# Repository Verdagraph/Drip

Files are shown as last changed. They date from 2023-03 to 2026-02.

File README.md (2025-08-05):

<!-- PROJECT SHIELDS -->
<!--
*** I'm using markdown "reference style" links for readability.
*** Reference links are enclosed in brackets [ ] instead of parentheses ( ).
*** See the bottom of this document for the declaration of the reference variables
*** https://www.markdownguide.org/basic-syntax/#reference-style-links
-->

[][version-url]
[][issues-url]
[][prs-url]

<!-- PROJECT LOGO -->
<br />
<div align="center">
  <a href="https://github.com/Verdagraph">
    
  </a>

<h3 align="center">Verdagraph - Web Application</h3>

  <p align="center">
    A garden productivity tool, agro-ecology model, and IoT platform
    for a sustainable and cooperative future.
    <br />
    <!-- 
    <a href=""><strong>Try it yourself »</strong></a>
    <br />
    -->
    <br />
    <a href="https://verdagraph.org">Documentation</a>
    <!-- 
    ·
    <a href="https://youtu.be/jGFHhRVdxRM">YouTube</a>
    ·
    <a href="">Donate</a>
    --> 
    <br />
  </p>
</div>

See the [main project readme](https://github.com/Verdagraph) for background on this repository.

The Drip is an IoT irrigation controller intended to automate the management of fixed-pressure water supplies along with variable-pressure / gravitypfed rain catchement systems. Its current scope is to control dispensing water from one rain barrel and one fixed pressure supply, using a flow meter to track precise targets, and a pressure sensor to track the water level of the catchement system, and an ESP32.

This repository contains the ESP-IDF firmware, PCB design, BOM, and instructions for setting up the system. 

Possible improvements, in no particular order:
    - Creating a solar charging version with included circuitry and deep sleep mode.
    - Support using more than one of each type of water supply.
    - Control 12V pumps in case gravity-fed isn't possible.

## PCB Design

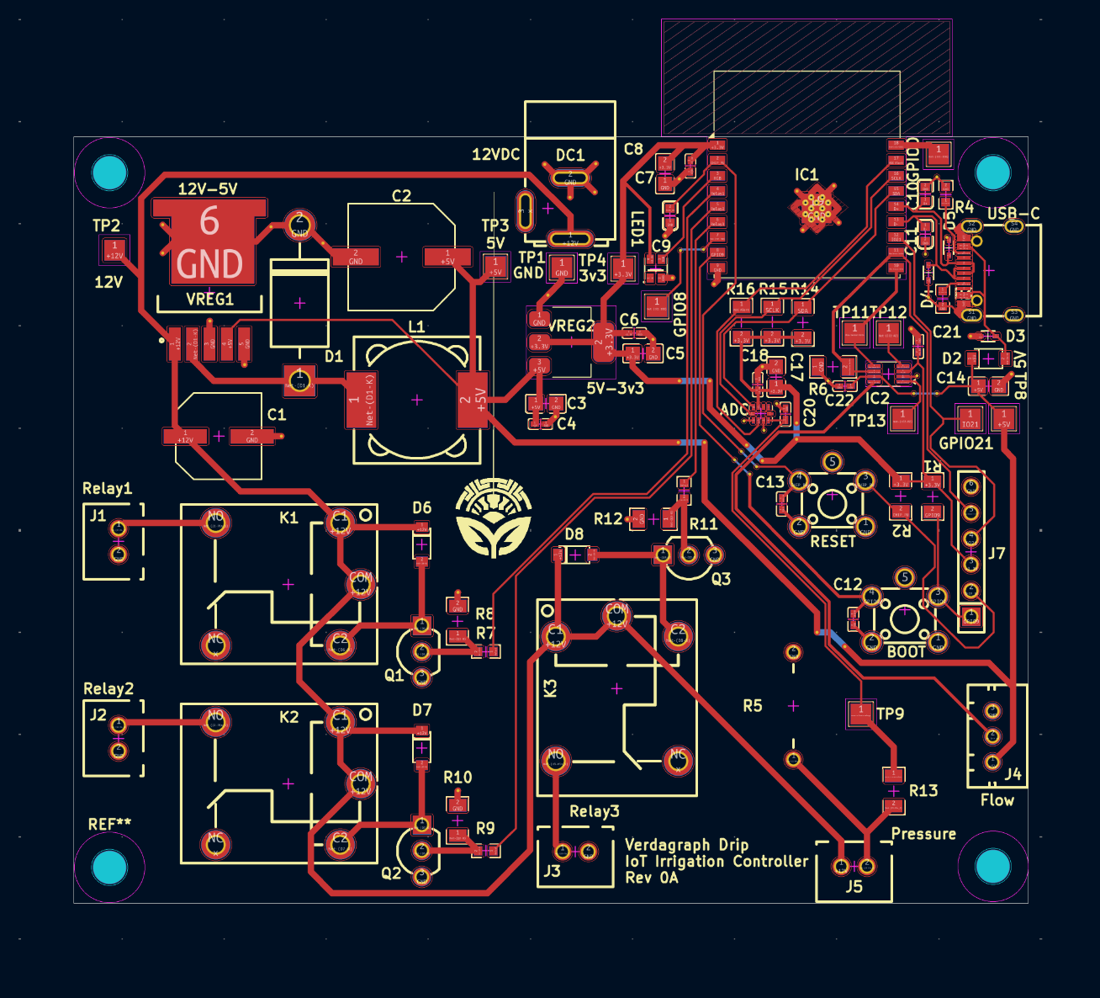
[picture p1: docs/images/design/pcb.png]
PCB Screenshot


## Firmware Design

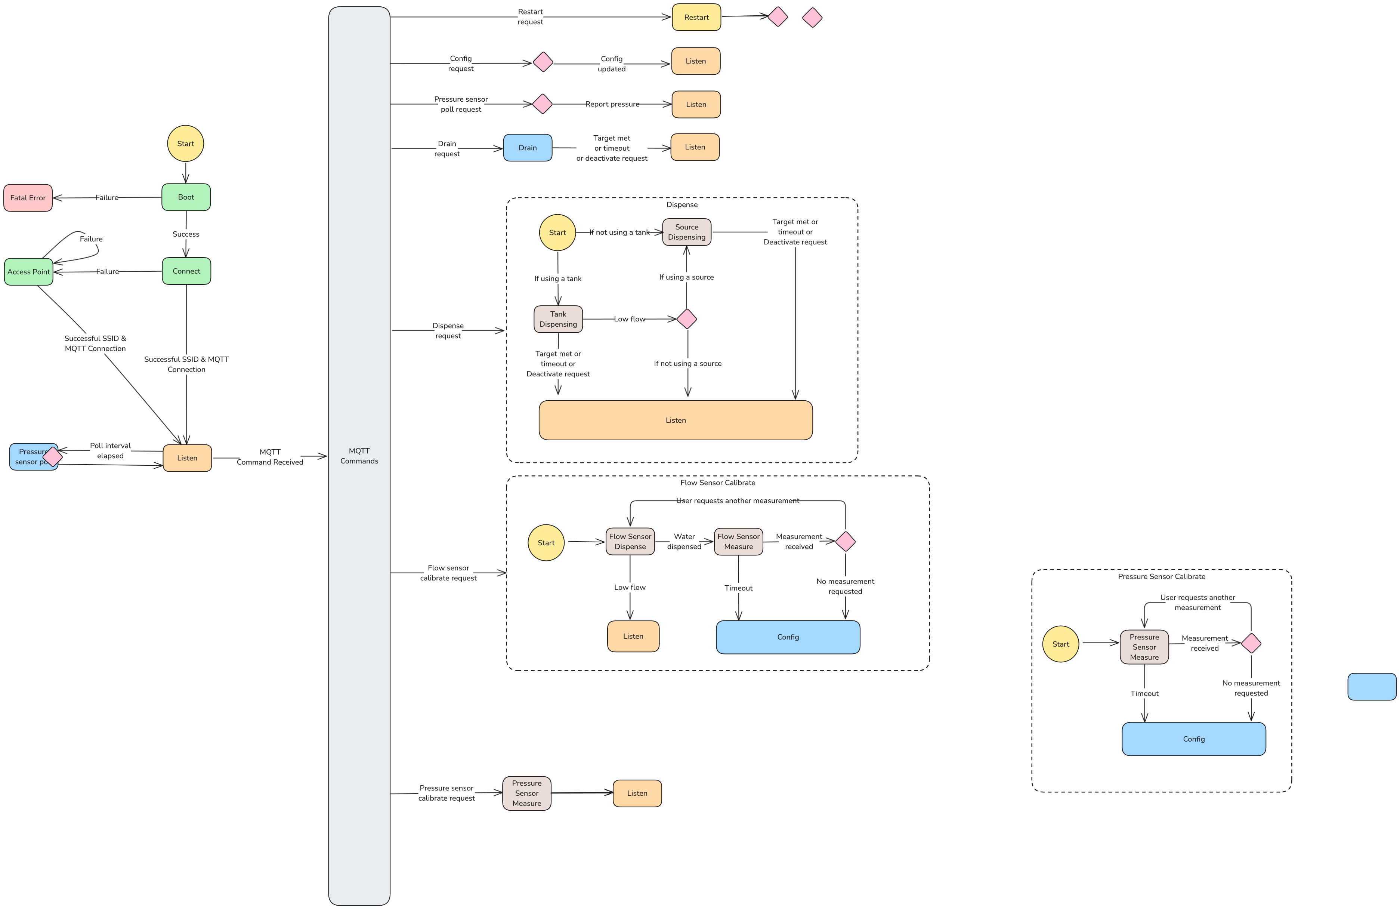
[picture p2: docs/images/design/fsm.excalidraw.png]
FSM Screenshot


# Contributing

See the [contributing](./contributing.md) for instructions on contributing and setting up the development environment.

<!-- MARKDOWN LINKS & IMAGES -->
<!-- https://www.markdownguide.org/basic-syntax/#reference-style-links -->

<!-- IN-REPO -->

[version-shield]: https://img.shields.io/badge/version-0.0.1-blue?style=for-the-badge
[version-url]: https://github.com/Verdagraph/Drip/releases
[issues-shield]: https://img.shields.io/github/issues/Verdagraph/Drip.svg?style=for-the-badge
[issues-url]: https://github.com/Verdagraph/Drip/issues
[prs-shield]: https://img.shields.io/github/issues-pr/Verdagraph/Drip.svg?style=for-the-badge
[prs-url]: https://github.com/Verdagraph/Drip/pulls
[license-shield]: https://img.shields.io/github/license/Verdagraph/Drip.svg?style=for-the-badge
[license-url]: https://github.com/Verdagraph/Drip/LICENSE.txt

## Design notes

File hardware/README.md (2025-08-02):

# PCB Design

https://www.electronics-tutorials.ws/blog/relay-switch-circuit.html
https://www.digikey.ca/en/blog/logic-level-shifting-basics  

There's two main type of pressure transducers: ones that have two wires and output a current, and ones that have 3 wires and output a voltage.
We can use the first type by adding a resistor with a known value to the path. Because we know the sensor is outputting a given current, and we know that the resistor must dissipate all the voltage before it as its connected to ground, we can take the voltage before the resistor and connect it to our ADC for a measurements.
The resistor is commonly 250 ohms which translates to 1-5V. For the voltage type, it is as simple as connecting the voltage to the ADC. For the current type, we measure the voltcage through a 10k ohm resistor, and remember that the 250 ohm resistor must sink the power (THT). We use a 220 ohm to give a little margin for error.

The reset button is connected to the CHIP_PU or chip power up pin on the ESP. It is pulled up by default, enabling the MCU. When the button is pressed it is pulled to GND, with a small filtering capacitor to smooth it out, and the device resets.

The boot button is connectod to GPIO9. When GPIO0 is pulled high, the chip will boot into its saved program. When its pulled low, it will enter into the USB/UART boot mode. This person (https://www.instructables.com/Build-Custom-ESP32-Boards-From-Scratch-the-Complet/) also added a pullup here and found it reduced boot errors.

The USBC receptable connects the positive and negative data terminals on either side together and shunts them along with the USB bus voltage with zener diodes for ESD protection and the schtokky diode on the voltage line for reverse current protection, along with a filtering capacitor. THe CC1 and CC2 lines are pulled down for USBC functinoality

To the microcontroller: the power line is again filtered so that the voltage regulators can be farther from the rest. The chip_pu is pulled up again and filtered. The USB data lines are filtered again as well. There is a common bug in the devkits where because the CHIP_EN pin is used to reset the chip, and the GPIO9 pin is used to select the boot mode, the GPIO9 pin must be high at least 3ms before the CHIP_EN pin to avoid puttin the board in boot. To accomplish this, we add a pullup to GPIO9 to get around the weak internal pullup. This works because the GPIO9 is pulled up to the 3v3 output of the regulator, but the CHIP_EN is only brouhgut up once the ESP's 3v3 rail stabalizes, and it has extra filtering capacitors so it takes longer.

Our 12v-5v regulator is a switching buck converter LM2575, the fixed 5V output version. According to the typical application circuit, it has a filtering capacitor on the input, an LC filter on the output. There is also a schtokky diode to ground which allows a path for the inductor transient response to dissipate. To choose the L we follow the datasheet. Vin - Vout = 12-5 = 7. Vin - Vout * Vout / Vin * 1000 / 52 = 56V x us. We use the figure 12 to find the intersection of this and 1A means 220uH is  good. To choose output cap we use the formula in the datasheet which yields 56 uF. This is only for stability though. For ripple We round up to 330. 

the 5V to 3.3V regulator is the AMS1117 linear regulator and it has the same 2 capacitor filter on either end with a power LED.

The relays. These are 5 terminal 5V relay modules. The coils need 5V and 360mw to turn on so they need .36 / 5 = 72ma to run. Except the CE has voltage at saturation so we factor in a 0.7V drop. We also double the minimum current we need to make sure it works which gives us 167mA. We need to drive it with a transistor to get the 5V signal. The relay has a flyback diode. We use the BC337 but assume the transistor to have abeta of at least 100 which will cover common transistors at these conditions. This gives us a base current of 1.67mA. Given we're using 3.3v to run this that means the voltage across the resistor must be (3.3V - VBE) = 3.3 - 1.2 (which is the max BE voltage on the BC337 and 2n2222a) = 2.1V. R = V / I = 2.1V / 1.67ma = 1254ohm rounded to 1000.

The flow sensor: we use the TX20102 logic level shifter to go between the 5V pulses of the flow sensor and the 3.3V logic of the ESP. The enable pin is pulled down and connected to a GPIO so we can disable the pulses into the microcontroller when we don't care about the flow. We also have 0.1uF filters to stabailize the reference voltages as much as possible.

The ADC is the ADC088S022, as the ESP ADC is not reliable. This has both the 5V and 3.3V lines as the analog and digital power lines with filtering. The I2C is used to communicate with the ESP, while the power lines are filted as well. The max that we can go on any input is the analog supply + 0.3V, meaning we shouldn't make it go beyond 5.3V

https://www.aliexpress.com/item/1005006568129795.html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

Power profiles:
ESP32c3 wroom 02: max 345A

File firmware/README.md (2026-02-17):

git clone --recursive <your-repo-url>

git submodule update --init --recursive

| Supported Targets | ESP32 | ESP32-C2 | ESP32-C3 | ESP32-C5 | ESP32-C6 | ESP32-C61 | ESP32-H2 | ESP32-H21 | ESP32-H4 | ESP32-P4 | ESP32-S2 | ESP32-S3 | Linux |
| --- | ----- | --- | --- | --- | --- | --- | --- | --- | --- | --- | --- | --- | ----- |

# Hello World Example

Starts a FreeRTOS task to print "Hello World".

(See the README.md file in the upper level 'examples' directory for more information about examples.)

## How to use example

Follow detailed instructions provided specifically for this example.

Select the instructions depending on Espressif chip installed on your development board:

- [ESP32 Getting Started Guide](https://docs.espressif.com/projects/esp-idf/en/stable/get-started/index.html)
- [ESP32-S2 Getting Started Guide](https://docs.espressif.com/projects/esp-idf/en/latest/esp32s2/get-started/index.html)

## Example folder contents

The project **hello_world** contains one source file in C language [hello_world_main.c](main/hello_world_main.c). The file is located in folder [main](main).

ESP-IDF projects are built using CMake. The project build configuration is contained in `CMakeLists.txt` files that provide set of directives and instructions describing the project's source files and targets (executable, library, or both).

Below is short explanation of remaining files in the project folder.

```
├── CMakeLists.txt
├── pytest_hello_world.py      Python script used for automated testing
├── main
│   ├── CMakeLists.txt
│   └── hello_world_main.c
└── README.md                  This is the file you are currently reading
```

For more information on structure and contents of ESP-IDF projects, please refer to Section [Build System](https://docs.espressif.com/projects/esp-idf/en/latest/esp32/api-guides/build-system.html) of the ESP-IDF Programming Guide.

## Troubleshooting

* Program upload failure

    * Hardware connection is not correct: run `idf.py -p PORT monitor`, and reboot your board to see if there are any output logs.
    * The baud rate for downloading is too high: lower your baud rate in the `menuconfig` menu, and try again.

## Technical support and feedback

Please use the following feedback channels:

* For technical queries, go to the [esp32.com](https://esp32.com/) forum
* For a feature request or bug report, create a [GitHub issue](https://github.com/espressif/esp-idf/issues)

We will get back to you as soon as possible.

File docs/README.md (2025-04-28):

# VerdanTech Drip - Open Source Drip Irrigation Controller

The VDT Drip is an open source irrigation controller based on the ESP8266. The Drip's main function is to dispense a given volume of water with irrigation systems that integrate variable-flow water supplies.

To do this, the Drip employs 1-3 solenoid valve(s), 0-1 flow sensor(s), 0-1 pressure sensor(s), and communication via an MQTT broker.

## Project Instructions

1. Read the [terminology](#terminology) and [interface](#mqtt-interface) sections 
to understand the device's capabilities and limitations.

2. Read the [hardware](#hardware) section and decide on an operating mode.

3. Secure the use of an MQTT broker

4. Source [materials](#equipment-1)

5. [Assemble](#assembly) the device

6. Install the Arduino platform, required libraries, and board drivers

7. Configure the device through the file `config.h`

8. Flash the microcontroller with the software

9. Connect to a WiFi network and MQTT broker through the auto-connect access point

10. Calibrate flow sensor

## Terminology

Refer to this list for explicit descriptions of some key terms used throughout the document.

### Water Supplies

- **Source**
    - A supply of water that is assumed to be inexhaustible with a static or variable flow rate, such as a utility water supply.
- **Tank**
    - A supply of water that is assumed to be exhaustible with a variable flow rate, such as a rain barrel.

### Equipment

For specific product examples see the [equipment](#equipment) section.

- **Valve**
    - An electronically controllable water valve, such as a solenoid valve.
- **Flow sensor**
    - A water flow sensor capable of sending a steady rate of electrical pulses per unit volume, such as a hall effect flow sensor.
- **Pressure sensor**
    - A pressure sensor capable of sending an absolute pressure reading through I2C and of surviving the maximum water pressure in the **Tank**.
- **Operational mode**
    - A specific combination of source, tank, valves, flow sensor, and pressure sensor, as described in the [hardware](#operating-modes) section.

### Software

- **MQTT**
    - A network protocol used for internet-of-things (IOT) devices. See [wiki](https://en.wikipedia.org/wiki/MQTT).

### Operation

- **Dispense**
    - A process of attempting to output a target volume of water, first from the tank, then from the source.
- **Drain**
    - A process of attempting to release water from the tank without it going to the usual intended output, to prevent overflow, or to get rid of stale water.

## MQTT interface

This section describes the functionality of the MQTT topics through which the device sends and recieves information. All communication is done via JSON. For topics which are subscribed to by the controller, a list of inputs is described for each topic, and for topics which are published by the controller, a list of outputs are described for each topic. Inputs are marked (optional) if the  function will still be carried out if they aren't included rather than throw an error. Inputs are marked (conditional) if they only have effect based on [configuration settings](#configuration), and outputs are marked (conditional) if their inclusion in the payload is dependent on [configuration settings](#configuration).

| Title | Topic string config  | Does the controller publish or subscribe? | Is the topic enabled unconditionally? |
| --- | --- | --- | --- |
| [Dispense activate](#activation)  | [`DISPENSE_ACTIVATE_TOPIC_`](#auto-config) | Subscribe | Yes |
| [Dispense slice report](#slice-reporting)  | [`DISPENSE_REPORT_SLICE_TOPIC_`](#auto-config)  | Publish | Yes |
| [Dispense summary report](#summary-reporting)  | [`DISPENSE_REPORT_SUMMARY_TOPIC_`](#auto-config)  | Publish | Yes |
| [Deactivate](#deactivation)  | [`DEACTIVATE_TOPIC_`](#auto-config)  | Subscribe | Yes |
| [Restart](#restart)  | [`RESTART_TOPIC_`](#auto-config)  | Subscribe | Yes |
| [Info logging](#info)  | [`LOG_TOPIC_`](#auto-config)  | Publish | Yes |
| [Warning logging](#warnings)  | [`WARNING_TOPIC_`](#auto-config)  | Publish | Yes |
| [Error logging](#errors)  | [`ERROR_TOPIC_`](#auto-config)  | Publish | Yes |
| [Read config](#read)  | [`CONFIG_TOPIC_`](#auto-config)  | Publish | Yes |
| [Read auto-config](#read-auto-config)  | [`AUTO_CONFIG_TOPIC_`](#auto-config)  | Publish | Yes |
| [Read topic config](#read-topic-config)  | [`TOPIC_CONFIG_TOPIC_`](#auto-config)  | Publish | Yes |
| [Write config](#write)  | [`CONFIG_CHANGE_TOPIC_`](#auto-config)  | Subscribe | Yes |
| [Reset settings](#reset-settings)  | [`SETTINGS_RESET_TOPIC_`](#auto-config)  | Subscribe | Yes |
| [Flow sensor calibrate begin](#begin) | [`FLOW_SENSOR_CALIBRATE_BEGIN`](#auto-config) | Subscribe | No |
| [Flow sensor calibrate dispense](#dispense) | [`FLOW_SENSOR_CALIBRATE_DISPENSE`](#auto-config) | Subscribe | No |
| [Flow sensor calibrate measure](#measure) | [`FLOW_SENSOR_CALIBRATE_MEASURE`](#auto-config) | Subscribe | No |
| [Drain activate](#activation-1)  | [`DRAIN_ACTIVATE_TOPIC_`](#auto-config)  | Subscribe | No |
| [Drain summary report](#reporting)  | [`DRAIN_REPORT_SUMMARY_TOPIC_`](#auto-config)  | Publish | No |
| [Pressure report request](#request)  | [`PRESSURE_REQUEST_TOPIC_`](#auto-config) | Subscribe | No |
| [Pressure report](#report) | [`PRESSURE_REPORT_TOPIC_`](#auto-config) | Publish | No |

### Dispense

The main functionality of the device. The dispentation topics handle setting target volumes for the dispense process, publishing data taken at regular intervals through the process, and publishing data at the end of the process.

#### Activation

| Topic string config  | Publish or subscribe? | Enabled unconditionally? |
| --- | --- | --- |
| [`DISPENSE_ACTIVATE_TOPIC_`](#auto-config)  | Subscribe | Yes |

This topic allows activating the dispense process and setting the target volume. Activation will fail if a dispense process or drain process is already in progress. The dispense process will continue until the output volume is greater than or equal to the target volume, or a singularly connected tank produces a flow rate less than that defined by [`FlowSensorConfig.min_flow_rate`](#runtime-config) and the current duration of the process is greater than that defined by [`TankConfig.tank_timeout`](#runtime-config). If the tank is connected with a source, then the dispense will switch to the source until the target volume is reached.

Inputs:
- `["tv"]` float. Target volume of the dispense process in liters.

Sample payload:
```
{
  "tv": 10.25
}
```

#### Slice Reporting

| Topic string config  | Publish or subscribe? | Enabled unconditionally? |
| --- | --- | --- |
| [`DISPENSE_REPORT_SLICE_TOPIC_`](#auto-config)  | Publish | Yes |

This topic is where the mid-process datapoints on the dispense process are published at a volume interval in liters defined by [`ServicesConfig.data_resolution_l`](#runtime-config). If the connection to the MQTT broker fails, these reports will fail to be sent and are lost, but the dispense process will continue. Unfortunately, the [MQTT client](#dependencies) class is only able to send messages at a quality-of-service of 0. 

Outputs:
- `["t"]` float. Current duration of the dispense process in seconds.
- `["v"]` float. Current output volume of the dispense process in liters.
- `["q"]` float. The average flow rate of output volume calculated either from the last slice report to the current one (or from the beginning of the process if on the first report) in liters per minute
- `["tp"]` (conditional) float. The average tank gauge pressure calculated from the last slice report to the current one (or from the beginning of the process if on the first report) in hectopascals. Enabled if [`USING_PRESSURE_SENSOR_`](#auto-config) and [`PressureSensorConfig.report_mode`](#runtime-config) equals 1 or 3.
- `["tv"]` (conditional) float. The average tank volume calculated from the last slice report to the current one (or from the beginning of the process if on the first report) in liters. Enabled if [`USING_PRESSURE_SENSOR_`](#auto-config) and [`PressureSensorConfig.report_mode`](#runtime-config) equals 2 or 3. Ensure that the [tank geometry](#runtime-config) is properly configured.

Sample payload:
```
{
  "t": 5000,
  "v": 0.1,
  "q": 13.2,
  "tp": 68.94,
  "tv": 85.6
}
```

#### Summary Reporting

| Topic string config  | Publish or subscribe? | Enabled unconditionally? |
| --- | --- | --- |
| [`DISPENSE_REPORT_SUMMARY_TOPIC_`](#auto-config)  | Publish | Yes |

This topic is where the post-process datapoints on the dispense process are published. If the connection to the MQTT broker fails, the connection is re-tried once before the message is lost.  Unfortunately, the [MQTT client](#dependencies) class is only able to send messages at a quality-of-service of 0.

Outputs:
- `["tt"]` float. Total duration of the dispense process in seconds.
- `["vt"]` float. Total output volume of the dispense process in liters.
- `["tv"]` (conditional) float. The total output volume produced by the tank in liters. Enabled if [`USING_TANK_`](#auto-config).
- `["tts"]` (conditional) int. The time stamp at which the dispense process switched from the tank to the source. Will equal `["tt"]` if the processes ended without switching water supplies. Enabled if [`USING_TANK_`](#auto-config) and [`USING_SOURCE_`](#auto-config).

Sample payload:
```
{
  "tt": 50,
  "vt": 10.25,
  "tv": 5.6,
  "tts": 250000,
}
```

### Deactivation

| Topic string config  | Publish or subscribe? | Enabled unconditionally? |
| --- | --- | --- |
| [`DEACTIVATE_TOPIC_`](#auto-config)  | Subscribe | Yes |

This topic is where commands for deactivating current processes are sent. Any message recieved on this topic will trigger the deactivation regardless of payload. Upon reception, the device will close all valves, end all ongoing dispense or drain processes, and send summary reports of any ongoing processes.

Inputs: None.

Sample payload:
```
{}
```

### Restart

| Topic string config  | Publish or subscribe? | Enabled unconditionally? |
| --- | --- | --- |
| [`RESTART_TOPIC_`](#auto-config)  | Subscribe | Yes |

This topic is where requests for restarting the controller are sent. Any message recieved on this topic will trigger the restart regardless of payload. Upon reception, the device will power down and restart, right after sending the reports for any processes in progress.

Inputs: None.

Sample payload:
```
{}
```

### Logging

These topics are where the device will send status logs alongside events and changes in state.

#### Info

| Topic string config  | Publish or subscribe? | Enabled unconditionally? |
| --- | --- | --- |
| [`LOG_TOPIC_`](#auto-config)  | Publish | Yes |

This topic is where the device sends status logs that aren't warnings or errors. Once connected to the MQTT broker, most status changes are reflected here. 

Outputs:
- `["m"]` string. The info log message.

Sample payload:
```
{
  "m": "Beginning dispense process with target volume: 10.25 liters"
}
```

#### Warnings

| Topic string config  | Publish or subscribe? | Enabled unconditionally? |
| --- | --- | --- |
| [`WARNING_TOPIC_`](#auto-config)  | Publish | Yes |

This topic is where the device sends status logs about events that don't break things but may result in abnormal function.

Outputs:
- `["m"]` string. The warning log message.

Sample payload:
```
{
  "m": "Flow rate exceeded maximum"
}
```

#### Errors

| Topic string config  | Publish or subscribe? | Enabled unconditionally? |
| --- | --- | --- |
| [`ERROR_TOPIC_`](#auto-config)  | Publish | Yes |

This topic is where the device sends status logs about events that prevent sucessful function.

Outputs:
- `["m"]` string. The error log message.

Sample payload:
```
{
  "m": "Dispense request denied, process already in progress."
}
```

### Config

These topics allow viewing and updating configuration settings at runtime, and viewing the hard-coded auto-configs. The available settings are listed as [config defaults](#defaults). 

#### Read

| Topic string config  | Publish or subscribe? | Enabled unconditionally? |
| --- | --- | --- |
| [`CONFIG_TOPIC_`](#auto-config)  | Publish | Yes |

This topic is where the device will send the current configuration values. It sends a retained message containing all values on startup and every time the configuration is changed.

Outputs:
- `["srvc"]["res"]` float. The value of [`ServicesConfig.data_resolution_l`](#runtime-config).
- `["src"]["rate"]` (conditional) float. The value of [`SourceConfig.static_flow_rate`](#runtime-config). Enabled if [`USING_SOURCE_`](#auto-config).
- `["tnk"]["time"]` (conditional) int. The value of [`TankConfig.tank_timeout`](#runtime-config). Enabled if [`USING_TANK_`](#auto-config).
- `["tnk"]["shape"]` (conditional) int. The value of [`TankConfig.shape_type`](#runtime-config). Enabled if [`USING_TANK_`](#auto-config).
- `["tnk"]["dim1"]` (conditional) float. The value of [`TankConfig.dimension_1`](#runtime-config). Enabled if [`USING_TANK_`](#auto-config).
- `["tnk"]["dim2"]` (conditional) float. The value of [`TankConfig.dimension_2`](#runtime-config). Enabled if [`USING_TANK_`](#auto-config).
- `["tnk"]["dim3"]` (conditional) float. The value of [`TankConfig.dimension_3`](#runtime-config). Enabled if [`USING_TANK_`](#auto-config).
- `["flow"]["ppl"]` (conditional) float. The value of [`FlowSensorConfig.pulses_per_l`](#runtime-config). Enabled if [`USING_FLOW_SENSOR_`](#auto-config).
- `["flow"]["max"]` (conditional) float. The value of [`FlowSensorConfig.max_flow_rate`](#runtime-config). Enabled if [`USING_FLOW_SENSOR_`](#auto-config).
- `["flow"]["min"]` (conditional) float. The value of [`FlowSensorConfig.min_flow_rate`](#runtime-config). Enabled if [`USING_FLOW_SENSOR_`](#auto-config).
- `["flow"]["time"]` (conditional) float. The value of [`FlowSensorConfig.calibration_timeout`](#runtime-config). Enabled if [`USING_FLOW_SENSOR_`](#auto-config).
- `["flow"]["cmax"]` (conditional) float. The value of [`FlowSensorConfig.calibration_max_volume`](#runtime-config). Enabled if [`USING_FLOW_SENSOR_`](#auto-config).
- `["prssr"]["mode"]` (conditional) int. The value of [`PressureSensorConfig.report_mode`](#runtime-config). Enabled if [`USING_PRESSURE_SENSOR_`](#auto-config).
- `["prssr"]["atmo"]` (conditional) float. The value of [`PressureSensorConfig.atmosphere_pressure`](#runtime-config). Enabled if [`USING_PRESSURE_SENSOR_`](#auto-config).
- `["auto"]["src"]` float. The value of [`USING_SOURCE_`](#auto-config).

Sample payload:
```
```

#### Read Auto-Config

| Topic string config  | Publish or subscribe? | Enabled unconditionally? |
| --- | --- | --- |
| [`AUTO_CONFIG_TOPIC_`](#auto-config)  | Publish | Yes |

This topic is where the device will send the hard-coded [auto-config](#auto-config) values, in a retained message. This topic is published to only on startup.

Outputs:
- `["src"]` bool. The value of [`USING_SOURCE_`](#auto-config).
- `["tnk"]` bool. The value of [`USING_TANK_`](#auto-config).
- `["drn"]` bool. The value of [`USING_DRAIN_VALVE_`](#auto-config).
- `["flow"]` bool. The value of [`USING_FLOW_SENSOR_`](#auto-config).
- `["prssr"]` bool. The value of [`USING_PRESSURE_SENSOR_`](#auto-config).
- `["srcpin"]` int. The value of [`SOURCE_OUTPUT_VALVE_PIN_`](#auto-config).
- `["tnkpin"]` int. The value of [`TANK_OUTPUT_VALVE_PIN_`](#auto-config).
- `["drnpin"]` int. The value of [`TANK_DRAIN_VALVE_PIN_`](#auto-config).
- `["flowpin"]` int. The value of [`FLOW_SENSOR_PIN_`](#auto-config).

Sample payload:
```
```

#### Read Topic Config

| Topic string config  | Publish or subscribe? | Enabled unconditionally? |
| --- | --- | --- |
| [`TOPIC_CONFIG_TOPIC_`](#auto-config)  | Publish | Yes |

This topic is where the device wil send the hard-coded [topic strings](#topics), in a retained message. Keep in mind that the strings are sent as they are before the appendment to [`BASE_TOPIC`](#topics), in order to minimize payload size. This topic is published to only on startup.

Outputs:
- `["base"]` string. The value of ['BASE_TOPIC'](#topics).
- `["out"]` string. The value of ['DISPENSE_ACTIVATE_TOPIC'](#topics).
- `["out_slice"]` string. The value of ['DISPENSE_REPORT_SLICE_TOPIC'](#topics).
- `["out_summary"]` string. The value of ['DISPENSE_REPORT_SUMMARY_TOPIC'](#topics).
- `["deactivate"]` string. The value of ['DEACTIVATE_TOPIC'](#topics).
- `["restart"]` string. The value of ['RESTART_TOPIC'](#topics).
- `["log"]` string. The value of ['LOG_TOPIC'](#topics).
- `["warning"]` string. The value of ['WARNING_TOPIC'](#topics).
- `["error"]` string. The value of ['ERROR_TOPIC'](#topics).
- `["config"]` string. The value of ['CONFIG_TOPIC'](#topics).
- `["auto"]` string. The value of ['AUTO_CONFIG_TOPIC'](#topics).
- `["topics"]` string. The value of ['TOPIC_CONFIG_TOPIC'](#topics).
- `["conf_write"]` string. The value of ['CONFIG_CHANGE_TOPIC'](#topics).
- `["conf_reset"]` string. The value of ['SETTINGS_RESET_TOPIC'](#topics).
- `["cbr_on"]` (conditional) string. The value of ['FLOW_SENSOR_CALIBRATE_BEGIN_TOPIC'](#topics). Enabled if [`USING_FLOW_SENSOR_`](#auto-config).
- `["cbr_out"]` (conditional) string. The value of ['FLOW_SENSOR_CALIBRATE_DISPENSE_TOPIC'](#topics). Enabled if [`USING_FLOW_SENSOR_`](#auto-config).
- `["cbr_measure"]` (conditional) string. The value of ['FLOW_SENSOR_CALIBRATE_MEASURE_TOPIC'](#topics). Enabled if [`USING_FLOW_SENSOR_`](#auto-config).
- `["drn"]` (conditional) string. The value of ['DRAIN_ACTIVATE_TOPIC'](#topics). Enabled if [`USING_DRAIN_`](#auto-config).
- `["drn_summary"]` (conditional) string. The value of ['DRAIN_REPORT_SUMMARY_TOPIC'](#topics). Enabled if [`USING_DRAIN_`](#auto-config).
- `["prssr_request"]` (conditional) string. The value of ['PRESSURE_REQUEST_TOPIC'](#topics). Enabled if [`USING_PRESSURE_SENSOR_`](#auto-config).
- `["prssr"]` (conditional) string. The value of ['PRESSURE_REPORT_TOPIC'](#topics). Enabled if [`USING_PRESSURE_SENSOR_`](#auto-config).

Sample payload:
```
```

#### Write

| Topic string config  | Publish or subscribe? | Enabled unconditionally? |
| --- | --- | --- |
| [`CONFIG_CHANGE_TOPIC_`](#auto-config)  | Subscribe | Yes |

This topic is where the device will accept changes to the configuration values. All the inputs are optional, meaning any combination of inputs will be accepted, and only the settings that are to be changed must be sent. Upon reception of the message, the device will update the [config structs](#runtime-config), write the new values to the file system, and publish the new values to [`CONFIG_TOPIC_`](#auto-config).

Inputs:
- `["srvc"]["res"]` (optional) float. The value of [`ServicesConfig.data_resolution_l`](#runtime-config) to be set.
- `["src"]["rate"]` (optional, conditional) float. The value of [`SourceConfig.static_flow_rate`](#runtime-config) to be set.
- `["tnk"]["time"]` (optional, conditional) int. The value of [`TankConfig.tank_timeout`](#runtime-config) to be set.
- `["tnk"]["shape"]` (optional, conditional) int. The value of [`TankConfig.shape_type`](#runtime-config) to be set.
- `["tnk"]["dim1"]` (optional, conditional) float. The value of [`TankConfig.dimension_1`](#runtime-config) to be set.
- `["tnk"]["dim2"]` (optional, conditional) float. The value of [`TankConfig.dimension_2`](#runtime-config) to be set.
- `["tnk"]["dim3"]` (optional, conditional) float. The value of [`TankConfig.dimension_3`](#runtime-config) to be set.
- `["flow"]["ppl"]` (optional, conditional) float. The value of [`FlowSensorConfig.pulses_per_l`](#runtime-config) to be set.
- `["flow"]["max"]` (optional, conditional) float. The value of [`FlowSensorConfig.max_flow_rate`](#runtime-config) to be set.
- `["flow"]["min"]` (optional, conditional) float. The value of [`FlowSensorConfig.min_flow_rate`](#runtime-config) to be set.
- `["flow"]["ctime"]` (optional, conditional) int. The value of [`FlowSensorConfig.calibration_timeout`](#runtime-config) to be set.
- `["flow"]["cmax"]` (optional, conditional) float. The value of [`FlowSensorConfig.calibration_max_volume`](#runtime-config) to be set.
- `["prssr"]["mode"]` (optional, conditional) int. The value of [`PressureSensorConfig.use_calibration`](#runtime-config) to be set.
- `["prssr"]["atmo"]` (optional, conditional) float. The value of [`PressureSensorConfig.atmosphere_pressure`](#runtime-config) to be set.

Sample payload:
```
```

### Flow Sensor Calibration

The flow sensor calibration topics allow taking volume measurments to calibrate the setting [`FlowSensorConfig.pulses_per_l`](#runtime-config). It's recommended that the output volume is captured as close as possible to the end of the flow sensor, to minimize the amount of fluid that is captured by the flow sensor but not the manual measurments. These topics only take inputs: reports on the status of the process use the [logging topics](#logging).

#### Begin

| Topic string config  | Publish or subscribe? | Enabled unconditionally? |
| --- | --- | --- |
| [`FLOW_SENSOR_CALIBRATE_BEGIN`](#auto-config) | Subscribe | No |

This topic allows starting and ending the flow calibration process. If no process is currently running, the controller will begin the process with the ID sent with the payload. The process will continue until it times out according to [`FlowSensorConfig.calibration_timeout`](), or until another message is recieved on this topic containing the same ID. The process will terminate without saving the calibrated value of [`FlowSensorConfig.pulses_per_l`](#runtime-config) if the process is stopped with the [deactivation topic](#deactivation).

Inputs:
- `["id"]` int. The id of the calibration process.

Sample payload:
```
```

#### Dispense

| Topic string config  | Publish or subscribe? | Enabled unconditionally? |
| --- | --- | --- |
| [`FLOW_SENSOR_CALIBRATE_DISPENSE`](#auto-config) | Subscribe | No |

This topic allows dispensing a given amount of fluid similarily to the usual dispense process. Unlike the usual dispense process, there is no switch from tank to source if both are being used: the source will be used the entire time. Once dispensed, the controller will wait until the measured volume is sent to the [measurment topic](#measure) before being able to start another dispense.

Inputs:
- `["id"]` int. The id of the calibration process. If the ID is incorrect or absent, no dispense will occur.
- `["tv"]` float. The target volume in liters. If this volume is greater than [`FlowSensorConfig.calibration_max_volume`](), no dispense will occur.

Sample payload:
```
```

#### Measure

| Topic string config  | Publish or subscribe? | Enabled unconditionally? |
| --- | --- | --- |
| [`FLOW_SENSOR_CALIBRATE_MEASURE`](#auto-config) | Subscribe | No |

This topic allows sending measurements to the calibration process. A total amount of pulses per liter and a count of pulses per liter measurments is maintained until the calibration process is ended, where it is then averaged and used to update the value of [`FlowSensorConfig.pulses_per_l`](#runtime-config).

Inputs:
- `["id"]` int. The id of the calibration process. If the ID is incorrect or absent, no measurment will be recorded.
- `["mv"]` float. The measured volume in liters. 

Sample payload:
```
```

### Reset Settings

| Topic string config  | Publish or subscribe? | Enabled unconditionally? |
| --- | --- | --- |
| [`SETTINGS_RESET_TOPIC_`](#auto-config)  | Subscribe | Yes |

This topic can be used to reset settings to their default values.

Inputs:
- `["wifi"]` (optional) bool. If `true`, run the function [`WiFiManager.resetSettings()`](#dependencies) and restart the ESP. The default auto-connect access point will return.
- `["mqtt"]` (optional) bool. If `true`, delete the MQTT config file and restart the ESP. The default [MQTT settings](#mqtt) will be used, and if the connection isn't successfull, the auto-connect access point will return.

Sample payload:
```
```

### Drain

The drain topics handle setting target times, pressures, or volumes for the drain process, publishing data at the end of the process. Enabled if `USING_DRAIN_VALVE_`. 

#### Activation

| Topic string config  | Publish or subscribe? | Enabled unconditionally? |
| --- | --- | --- |
| [`DRAIN_ACTIVATE_TOPIC_`](#auto-config)  | Subscribe | No |

This topic allows activating the drain process and setting either the target time, pressure, or volume. Activation will fail if a drain process or dispense process is already in progress. While inputs are listed as optional, the process will only start if exactly one target is sent. The drain process will continue until the duration of the process is greater than or equal to the target time, the tank gauge pressure is less than or equal to the target pressure, or the tank volume is less than or equal to the target volume, depending on which target was sent.

Inputs:
- `["tt"]` (optional) int. Target time of the drain process in seconds.
- `["tp"]` (optional, conditional) float. Target pressure of the drain process in hectopascals. Enabled if `USING_PRESSURE_SENSOR_`.
- `["tv"]` (optional, conditional) float. Target volume of the drain process in liters. Enabled if `USING_PRESSURE_SENSOR_`. Ensure that the [tank geometry](#runtime-config) is properly configured.

Sample payload:
```
```

#### Summary Reporting

| Topic string config  | Publish or subscribe? | Enabled unconditionally? |
| --- | --- | --- |
| [`DRAIN_REPORT_SUMMARY_TOPIC_`](#auto-config)  | Publish | No |

This topic is where the post-process datapoints on the drain process are published. If the connection to the MQTT broker fails, the connection is re-tried once before the message is lost. Unfortunately, the [MQTT client](#dependencies) class is only able to send messages at a quality-of-service of 0.

Outputs:
- `["tt"]` float. Total duration of the drain process in seconds.
- `["sp"]` (conditional) float. The inital tank gauge pressure of the drain process in hectopascals. Enabled if [`USING_PRESSURE_SENSOR_`](#auto-config) and [`PressureSensorConfig.report_mode`](#runtime-config) equals 1 or 3.
- `["fp"]` (conditional) float. The final tank gauge pressure of the drain process in hectopascals. Enabled if [`USING_PRESSURE_SENSOR_`](#auto-config) and [`PressureSensorConfig.report_mode`](#runtime-config) equals 1 or 3.
- `["sv"]` (conditional) float. The inital tank volume of the drain process in liters. Enabled if [`USING_PRESSURE_SENSOR_`](#auto-config) and [`PressureSensorConfig.report_mode`](#runtime-config) equals 2 or 3. Ensure that the [tank geometry](#runtime-config) is properly configured.
- `["fv"]` (conditional) float. The final tank volume of the drain process in liters. Enabled if [`USING_PRESSURE_SENSOR_`](#auto-config) and [`PressureSensorConfig.report_mode`](#runtime-config) equals 2 or 3. Ensure that the [tank geometry](#runtime-config) is properly configured.

Sample payload:
```
```

### Pressure

These topics allow publishing values for tank pressure and volume, as well as requesting these values be sent. Enabled if [`USING_PRESSURE_SENSOR_`](#auto-config).

#### Request

| Topic string config  | Publish or subscribe? | Enabled unconditionally? |
| --- | --- | --- |
| [Pressure report request](#request)  | [`PRESSURE_REQUEST_TOPIC_`](#auto-config) | Subscribe | No |

This topic is where pressure reports can be requested. Any message on this topic will cause the controller to publish the tank pressure, volume, or both, to the [pressure report topic](#report), depending on the value of [`PressureSensorConfig.report_mode`](#runtime-config).

Inputs: None.

Sample payload:
```
{}
```

#### Report

| Topic string config  | Publish or subscribe? | Enabled unconditionally? |
| --- | --- | --- |
| [Pressure report](#report) | [`PRESSURE_REPORT_TOPIC_`](#auto-config) | Publish | No |

This topic is where pressure reports are published. Pressure reports are published on device startup, before and after all dispense and drain processes, and when a message is recieved on the [pressure report request topic](#request).

Outputs:
- `["tp"]` (conditional) float. Gauge pressure in the tank in hectopascals. Enabled if [`PressureSensorConfig.report_mode`](#runtime-config) equals 1 or 3.
- `["tv"]` (conditional) float. Volume of water in the tank in liters. Enabled if [`PressureSensorConfig.report_mode`](#runtime-config) equals 2 or 3. Ensure that the [tank geometry](#runtime-config) is properly configured.

Sample payload:
```
```

# Hardware

## Operating Modes

source
tank
source + tank with using_source_flow as false
source + tank with using_source_flow as true

tank with drain valve
tank with pressure sensor 
tank with overflow 

fluid system components

## Equipment

In this section, I'll list all the equipment I used for this project. This isn't an exhaustive list of all parts that could be used: it's just a list of parts I used, and I build a controller with a source, tank, flow sensor, pressure sensor, and drain. The substitution of some parts, like the type of tubes and fittings, are simple, but other parts, like the microcontroller and sensors, will require significant modifications to the software.

Several of the items are 3D printed. You can find the 3D mesh (.stl) and the Fusion360 (.f3d) files in the CAD folder of the project directory. Unless you're using the exact same products as I am, the 3D models likely won't work for you, and you may find them inadequate in other aspects. Unfortunately, at the time I created these models, I didn't have knowledge of best practices for Fusion360, and so you may have a hard time modifying them for your purposes. Hopefully for those who start from scratch, my models will help, and please let me know if you create any so we can add them to the repo.

Each section will have a table in this format for summary:

| Item | Quantity | Where to source | Product Link |
| ---  | --- | --- | --- |
| Name of the item  | Will vary depending on other equipment and the scale of the irrigation network | Where I sourced it | The exact product I used |

### Core

These items form the core functionality of the device.

| Item | Quantity | Where to source | Product Link |
| ---  | --- | --- | --- |
| [Microcontroller](#microcontroller)  | 1 | Hobby shop | [Adafruit](https://www.adafruit.com/product/2471) |
| [Solenoid valve](#solenoid-valve) | 1 | Hobby shop | [BC Robotics](https://bc-robotics.com/shop/12v-solenoid-valve-34/) |
| [Solenoid valve (no minimum pressure)](#solenoid-valve-no-minimum-pressure) | 0-2 | Hobby shop | [BC Robotics](https://bc-robotics.com/shop/12v-solenoid-valve-no-minimum-pressure-34/) |
| [Flow sensor](#flow-sensor)  | 0-1 | Hobby shop | [Digiten](https://www.digiten.shop/products/digiten-g3-8-water-flow-hall-sensor-switch-flow-meter-0-3-10l-min) |
| [Pressure sensor](#pressure-sensor) | 0-1 | Hobby shop | [Adafruit](https://www.adafruit.com/product/3965) |

#### Microcontroller

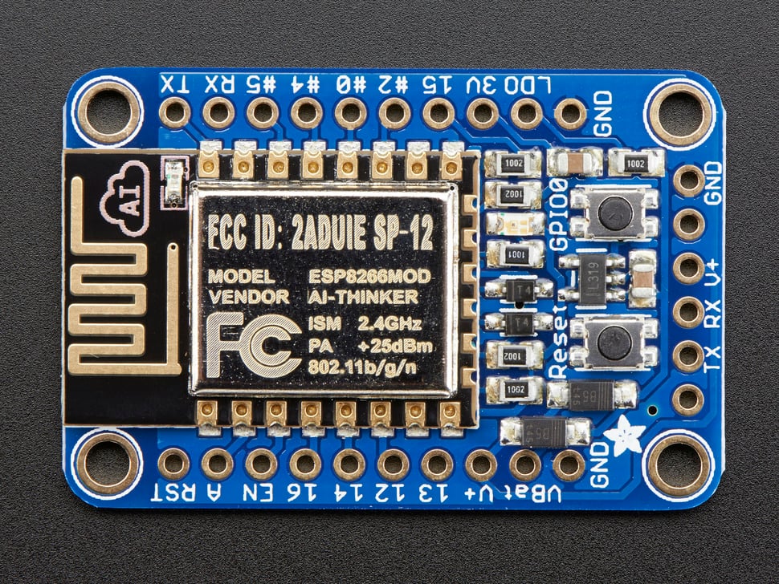
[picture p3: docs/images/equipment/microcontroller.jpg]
The ESP8266 microcontroller


The brains of the controller. **Required for every project.** I used the ESP8266 because of its price, availability, ease of programming, and most importantly: built-in WiFi. If you're using a different microcontroller, you will need to modify the software. The controller has some pin requirements you'll need to keep in mind if you're not using the Adafruit ESP I used:

- Enough pins for each of the valve(s).
- Interrupt capable pin (if [`USING_FLOW_SENSOR_`](#auto-config)).
- I2C pins (if [`USING_PRESSURE_SENSOR_`](#auto-config)).
- Deep sleep capability (if using [`AP_RETRY_DEEP_SLEEP`](#wifi-manager)).

#### Solenoid Valve

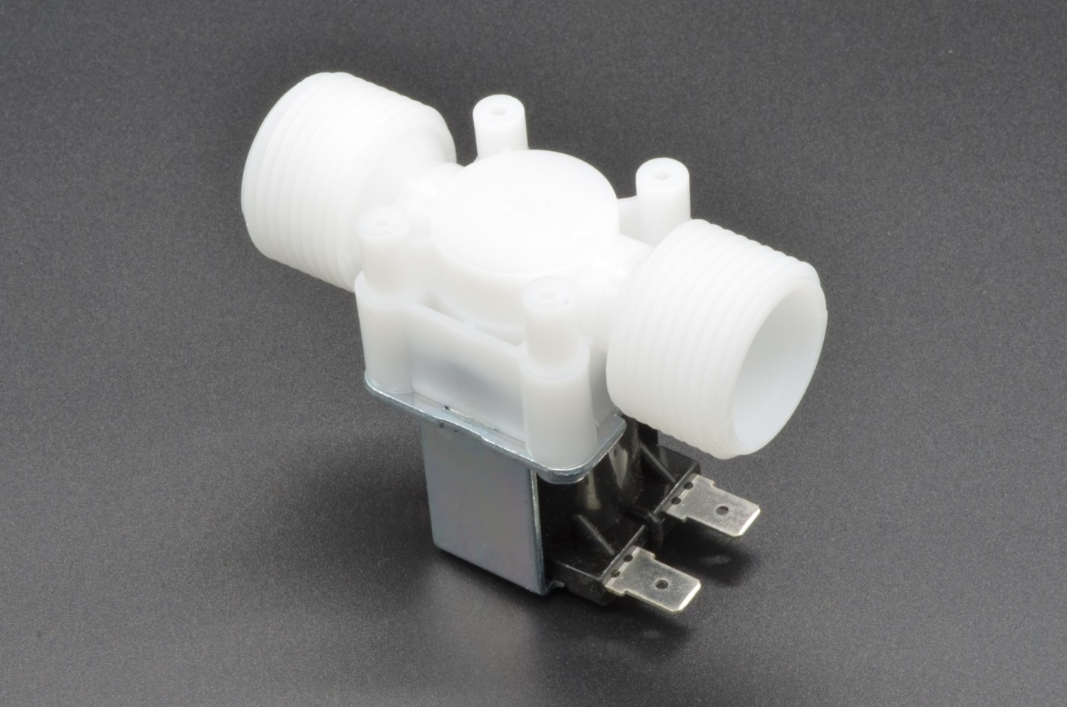
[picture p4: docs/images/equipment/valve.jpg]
A 12V solenoid valve


The main mechanical function of the device. **Required if [`USING_SOURCE_`](#auto-config).** These valves, which have a minimum pressure requirement to open/close, are suitable for use with a source, but not a tank, because a source is assumed to have a high enough pressure at all times. I used a 12V solenoid valve because I had a 12V power supply and it seemed a suitable choice. Keep in mind that for every valve you will need a [diode](#diode) to prevent EMF feedback, and that you will need a [relay](#relay) with a rated voltage that matches the valve's voltage, with at least as many modules as valves. 

#### Solenoid Valve (No Minimum Pressure)

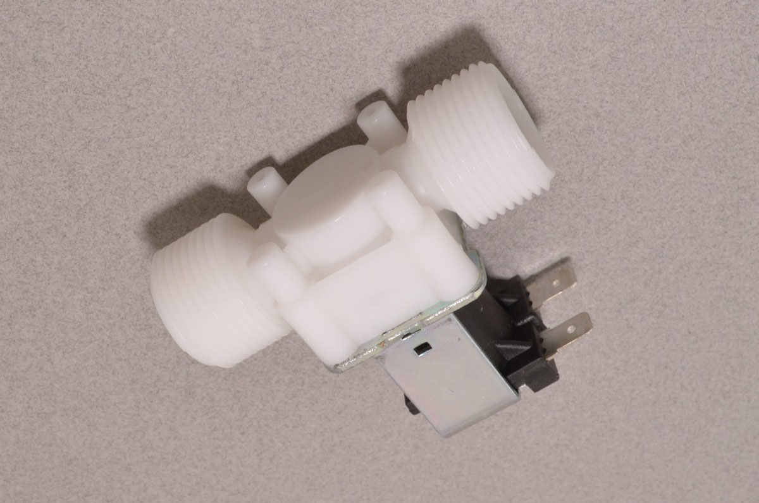
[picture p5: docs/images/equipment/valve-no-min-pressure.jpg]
A 12V solenoid valve with no minimum pressure


The main mechanical function of the device. **Required if [`USING_TANK_`](#auto-config).** These valves, which do not have a minimum pressure requirement to open/close, are suitable for use with a tank and a source, because a tank is assumed to possibly have zero pressure. I used a 12V solenoid valve because I had a 12V power supply and it seemed a suitable choice. Keep in mind that for every valve you will need a [diode](#diode) to prevent EMF feedback, and that you will need a [relay](#relay) with a rated voltage that matches the valve's voltage, with at least as many modules as valves. 

If you want to be able to drain fluid from your tank without having it go into your irrigation system, you'll need two of these valves: one output valve, and one drain valve. The output valve is of course necessary for all setups with a tank, but the drain valve may not be necessary depending on your requirements. I chose to use one because, from what I understand, you're not supposed to let water sit stale in a rain barrel for more than 10 days or so, and I wanted to automate that. I also combined the tank drain with a simple overflow tube running out of the top of the barrel, to ensure that it doesn't overflow even if the controller didn't have power to open the drain valve. More details in the [operating modes](#operating-modes) section and the [assembly](#assembly) section. 

#### Flow Sensor

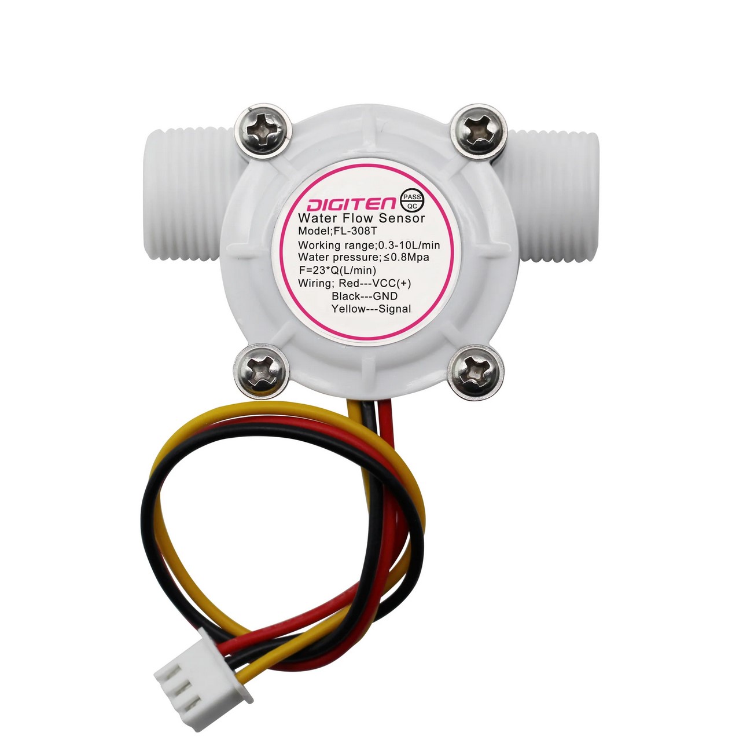
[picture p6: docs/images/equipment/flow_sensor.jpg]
A hall effect flow sensor


Used for sensing the rate of water flow through the tank's output, or the tank and source's output. **Required if [`USING_TANK_`](#auto-config) or if [`USING_SOURCE_`](#auto-config) and [`USING_SOURCE_FLOW`](#core-1).** The flow sensor I used is a hall effect flow sensor, which uses a magnetic field to send voltages pulses into a data wire. 
I used the sensor I did because the flow rate range (0.6-10L/min) seemed like it would capture what would be coming out of my water supplies, and because the 3/8 inch thread was convienent to make [adapters](#38-thread-to-34-thread) for.

The sensor uses an interrupt pin to update the controller's memory, specifically a `volatile int.` The sensor that I used runs on a logic level of 5V, which was too high for the 3.3V level of the ESP8266. Make sure you either find a flow sensor with a logic level that matches the microcontroller, or use a [logic level shifter](#logic-level-converter) or some alternative. 

Make sure to configure [`MAX_FLOW_RATE_DEFAULT`](#defaults) and [`MIN_FLOW_RATE_DEFAULT`](#defaults) for the sensor you choose.

#### Pressure Sensor

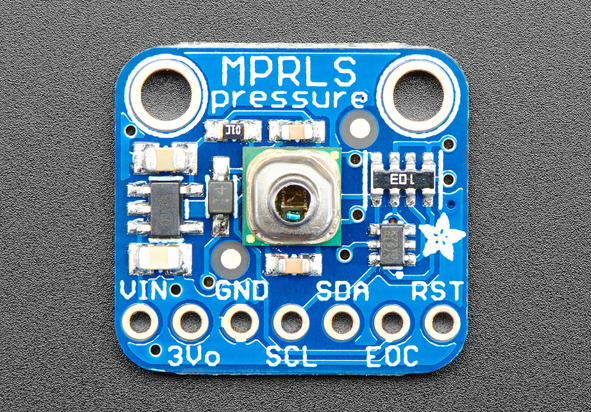
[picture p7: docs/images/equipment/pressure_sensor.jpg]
A ported pressure sensor


Used for sensing the absolute pressure in the tank. **Not required.** By subtracting the atmospheric pressure, defined by [`PressureSensorConfig.atmosphere_pressure`](#runtime-config), from the absolute pressure returned by the pressure sensor, we can get the gauge pressure in the tank. By configuring the [tank geometry](#runtime-config), we can estimate the volume of water in the tank. This is useful for a few reasons. First, we can keep track of how much water we have in the tank through the [pressure report topic](#report). If we're not using a source, this will tell us whether our irrigation controller can even output any water at all, and if we need to top up the tank or water the garden ourselves. Second, knowing the amount of water in our tank will allow us to know how long water has been sitting in it - allowing us to drain the tank, either with a [drain valve](#solenoid-valve-no-minimum-pressure), or manually - to prevent the growth of harmful organisms in the water.

When it comes down to it, the pressure sensor's only function is to tell us how much water there is in the tank. I chose the sensor I did because it was the only pressure sensor I could find on the website I ordered my other parts from, and while it doesn't explicitly say it's compatible with water pressure, I figured it would work because it uses a port which can be sealed and a silicon gel coating over the sensor pad. You may find it better to use another sensor specifically designed for water, which will require modifications to the software, as currently it assumes the use of a pressure sensor that returns the absolute pressure at the bottom of the tank in hectopacals through I2C. If you do use the sensor I did, keep in mind that it'll require some sort of [case](#pressure-sensor-case) to be able to connect to the tank. 

### Cases

These items are protective cases around the other items. Most are optional. How much moisture your components will have to handle will determine whether you should use a case. I happened to setup my rain barrel on a side of my house sheltered from the wind and rain, and the components directly underneath, so I'm testing these under relatively low stress. I recommend trying to place your setup in a similar area. 

| Item | Quantity | Where to source | Product Link |
| ---  | --- | --- | --- |
| [Controller case](#controller-case) | 1 | 3D Print | CAD folder |
| [Valve case](#valve-case) | 0-3 | 3D Print | CAD folder |
| [Flow sensor case](#flow-sensor-case) | 0-1 | 3D Print | CAD folder |
| [Pressure sensor case](#pressure-sensor-case) | 0-1 | 3D Print | CAD folder |
| [M3 screws](#m3-screws) | 0-1 | Hardware store | [Amazon](https://www.amazon.ca/gp/product/B01J7NM9JA/ref=ppx_yo_dt_b_asin_title_o07_s02?ie=UTF8&psc=1) |

#### Controller Case

Controller case

This case holds the proto-board circuit ([microcontroller](#microcontroller), [voltage regulator](#voltage-regulator), and [logic level converter](#logic-level-converter)) along with the relay. **Required for every project**. The included model screws in using 8 [M3 screws](#m3-screws), with two mounting holes for larger screws, and has a hole for a [power supply adapter](#power-supply-adapter) and a [cable gland](#cable-gland).

#### Valve Case

Valve case

This case fits both the [solenoid valve](#solenoid-valve) and the [no minimum pressure solenoid valve](#solenoid-valve-no-minimum-pressure), with a hole for a [2-wire waterproof connector](#2-wire-waterproof-connector). *Not required.* The valves are well constructed and don't appear to require a case. I decided to use one because I wanted to be safe and because I soldered both the diode and the connector directly onto the terminals of the valve, which didn't seem like a resilient way to join them. If you choose not to use a case, I'd recommend looking into how to get a sturdy and environment-proof connection on the valve terminals.

Screws in using 4 [M3 screws](#m3-screws).

#### Flow Sensor Case

Flow sensor case

This case fits the [flow sensor](#flow-sensor) and the [4-wire waterproof connector](#4-wire-waterproof-connector). **Not required.** The flow sensor's shell is well-constructed but I wanted to ensure the sensor would be protected from the environment.

Screws in using 4 [M3 screws](#m3-screws).

#### Pressure Sensor Case

Pressure sensor case

This case fits the [pressure sensor](#pressure-sensor), a cable of the [4-wire waterproof connector](#4-wire-waterproof-connector), and a 1/4 inch tube. **Required if [`USING_PRESSURE_SENSOR_`](#auto-config).** This case was my attempt to utilize the port on the sensor to measure water pressure. The port pressure fits into a hole on the bottom of the top half of the case, which is connected to an enclosed 1/4 inch hose barb. Being tightly fitted into the case, the pressure sensor is very easy to break by snapping off sensor from the board and the port from the sensor. I recommend fitting the port into the case as close as possible to closing up the device.

In order to waterproof as much as possible, I sprayed both sides of the case with an epoxy coating, and I placed small strips of electrical tape over the port and board of the pressure sensor.

Screws in using 4 [M3 screws](#m3-screws).

#### M3 screws

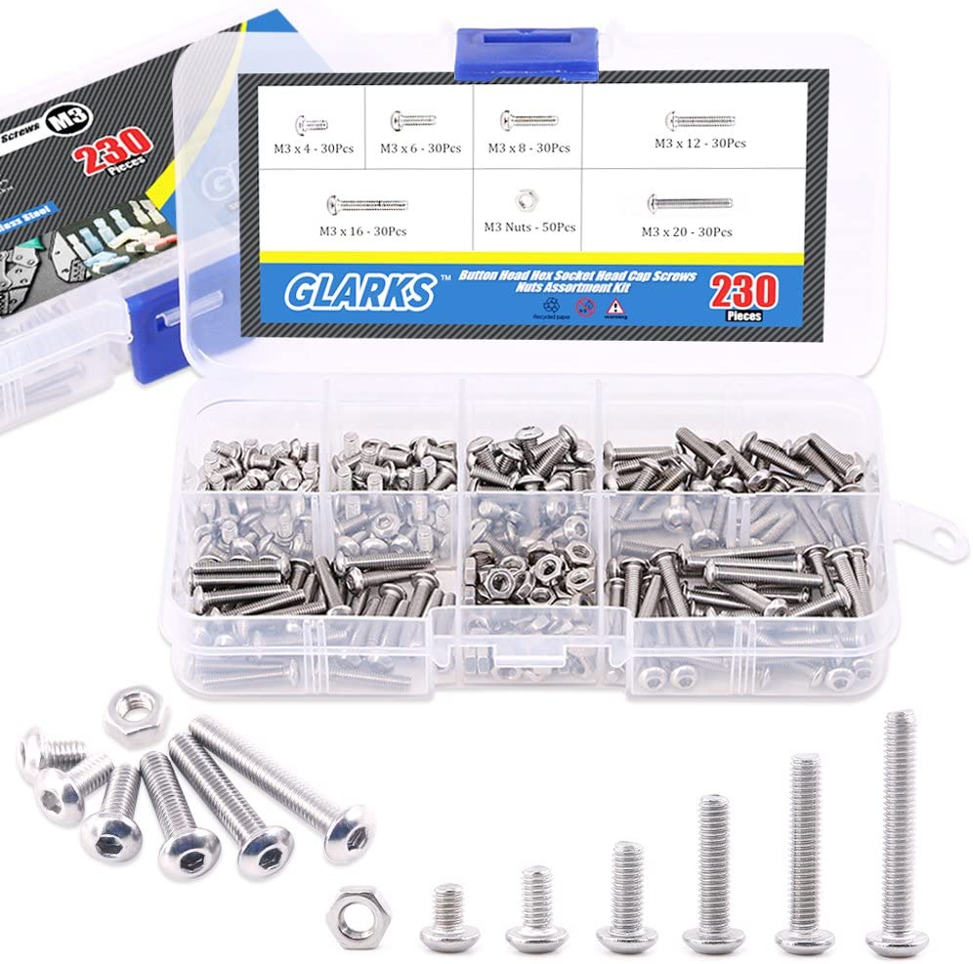
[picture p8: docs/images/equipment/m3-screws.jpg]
M3 screws


Used to fit together cases. **Required if using any cases.** There isn't a specific length of screw required by any of the cases, so any assortment of M3 screw lengths can be used. 

### Electrical

These items are electrical components needed to build the control circuit.

This section assumes you already has a soldering setup, solder, and wires

| Item | Quantity | Where to source | Product Link |
| ---  | --- | --- | --- |
| [Relay](#relay) | 1 | Hobby shop | [BC Robotics](https://bc-robotics.com/shop/4-channel-relay-breakout-12v/) |
| [Power supply](#power-supply) | 1 | Hobby shop | [BC Robotics](https://bc-robotics.com/shop/12v-3a-power-supply-2-5mm/) |
| [Power supply adapter](#power-supply-adapter) | 1 | Hobby shop | [BC Robotics](https://bc-robotics.com/shop/dc-barrel-jack-to-2-pin-terminal-block-adapter/) |
| [Voltage regulator](#voltage-regulator) | 1 | Hobby shop | [BC Robotics]() |
| [Diode](#diode) | 1-3 | Hobby shop | [BC Robotics](https://bc-robotics.com/shop/diode-rectifier-1a-50v/) |
| [Logic level converter](#logic-level-converter) | 0-1 | Hobby shop | [BC Robotics](https://bc-robotics.com/shop/4-channel-logic-level-converter-bi-directional/) |
| [Proto Board](#proto-board) | 1 | Hobby shop | [BC Robotics](https://bc-robotics.com/shop/1591l-proto-board/) |
| [2-wire waterproof connector](#2-wire-waterproof-connector) | 0-3 | Hobby shop | [BC Robotics](https://bc-robotics.com/shop/waterproof-dc-power-cable-set/) |
| [4-wire waterproof connector](#4-wire-waterproof-connector) | 0-2 | Hobby shop | [BC Robotics](https://bc-robotics.com/shop/waterproof-polarized-4-wire-cable-set/) |
| [Cable gland](#cable-gland) | 0-1 | Hobby shop | [BC Robotics](https://bc-robotics.com/shop/cable-gland-pg-9/) |

#### Relay

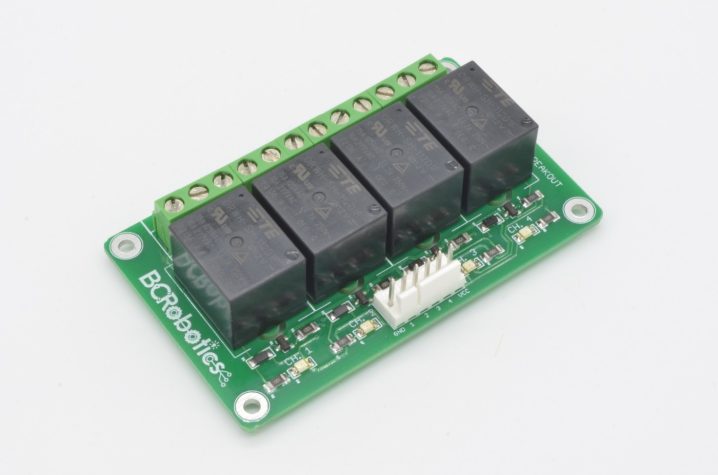
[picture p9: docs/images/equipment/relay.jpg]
12V relay


Used for switching the high voltage valves with the low voltage of the microcontroller. **Required for every project**. You will need a relay with a rated voltage that matches the valve's voltage, with at least as many modules as valves. The product I linked is a 4-module relay, because I'm using 3 valves and I couldn't find a 3-module relay. Make sure to test that your relay modules work, as I've had some bad luck in the past with recieving dead relays.

#### Power Supply

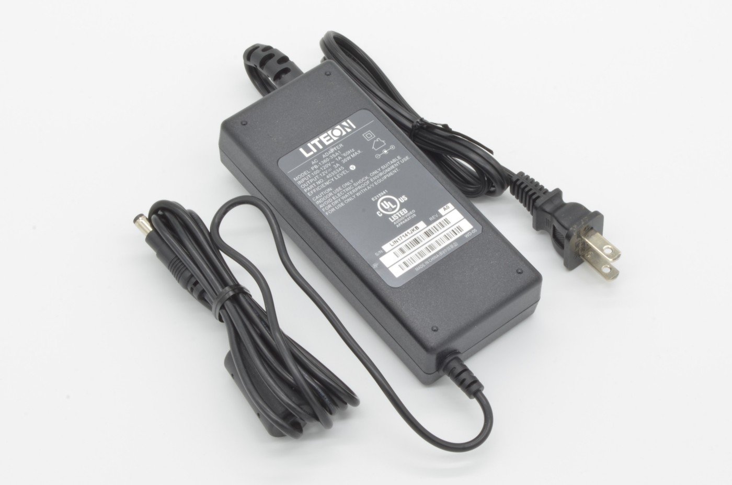
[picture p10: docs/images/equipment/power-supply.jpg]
12V power supply


#### Power Supply Adapter

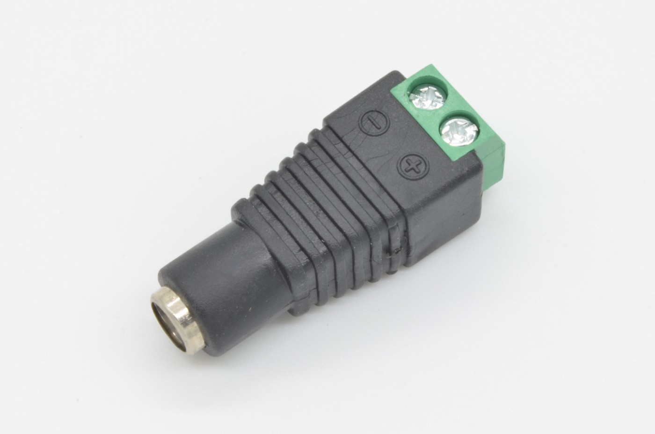
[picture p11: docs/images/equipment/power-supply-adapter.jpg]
Power supply adapter


#### Voltage Regulator

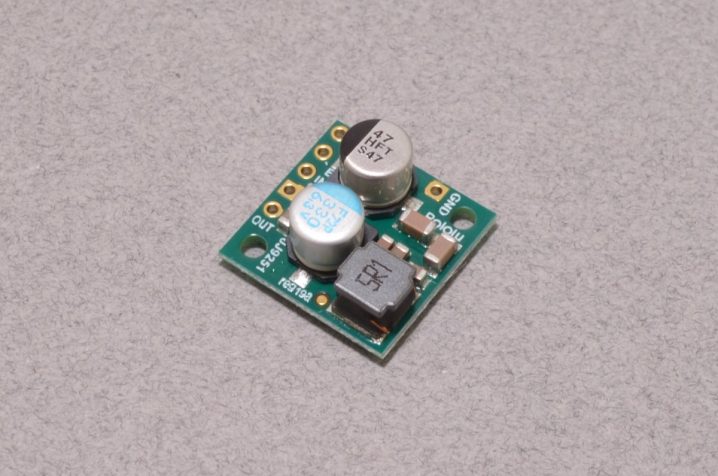
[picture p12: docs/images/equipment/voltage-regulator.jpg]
5V voltage regulator


#### Diode

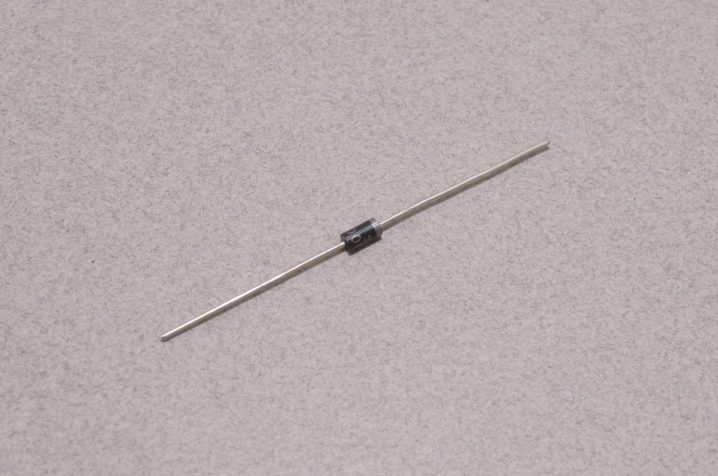
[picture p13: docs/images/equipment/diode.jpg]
Diode


#### Logic Level Converter

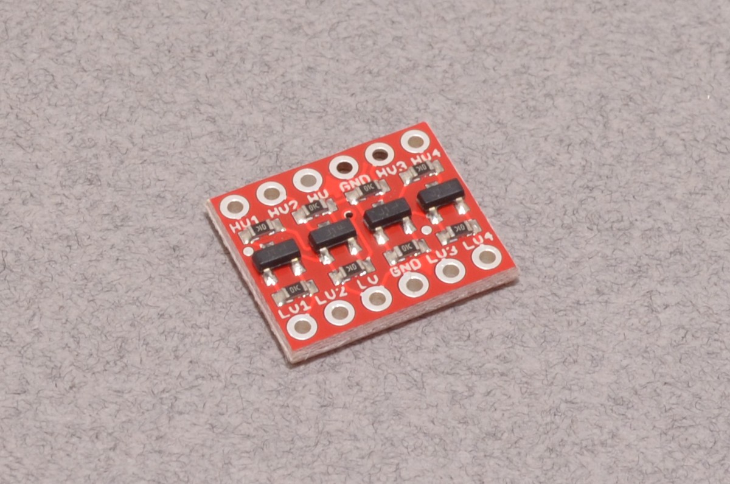
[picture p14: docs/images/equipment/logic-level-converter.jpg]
Logic level converter


#### Proto Board

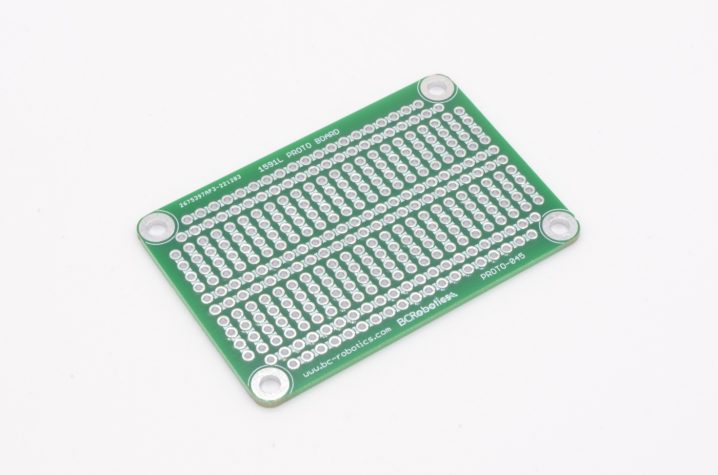
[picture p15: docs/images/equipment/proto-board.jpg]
Proto-board


#### 2-Wire Waterproof Connector

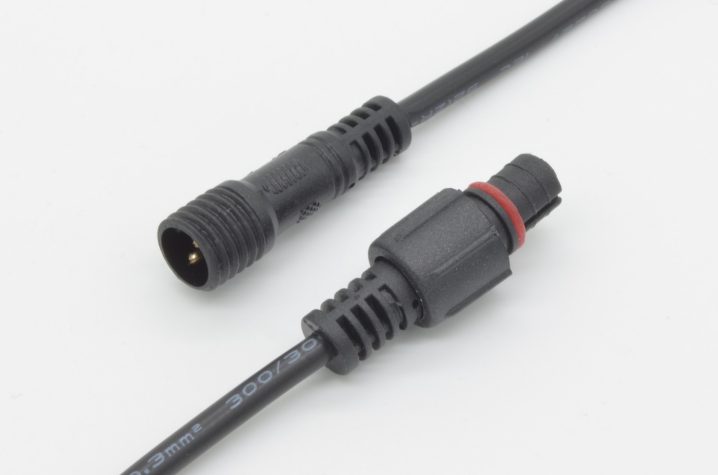
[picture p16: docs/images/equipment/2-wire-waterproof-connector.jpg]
2-wire waterproof connector


#### 4-Wire Waterproof Connector

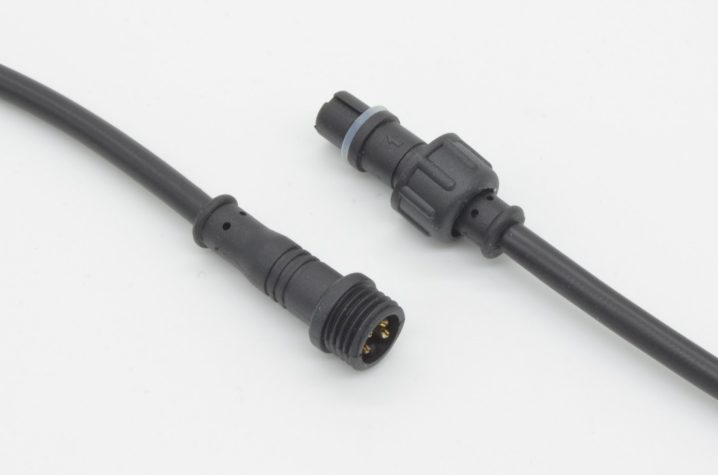
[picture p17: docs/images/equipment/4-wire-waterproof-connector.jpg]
4-wire waterproof connector


#### Cable Gland

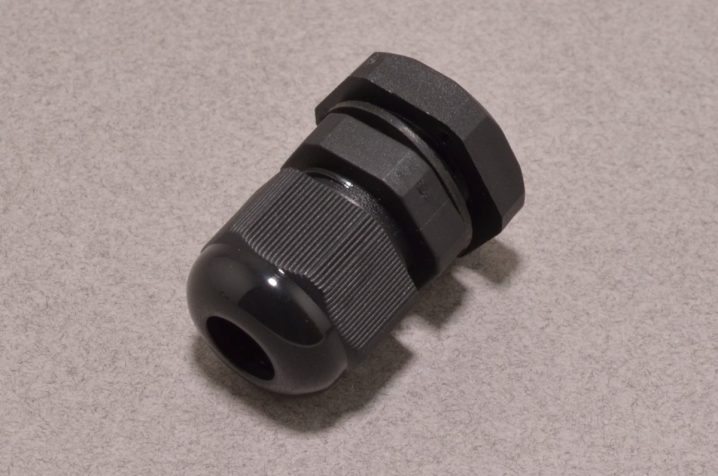
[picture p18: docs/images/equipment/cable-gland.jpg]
Cable gland


### Fluids

These items are needed to handle the water from the water supplies.

| Item | Quantity | Where to source | Product Link |
| ---  | --- | --- | --- |
| [1/2 poly](#12-poly) | 1+ | Irrigation supplier | [Irrigation Direct](https://www.irrigationdirect.ca/DD-DH700-100-1-2-x-100-.700-OD-Poly-Tubing-100-Roll-DD-DH700-100) |
| [1/4 poly](#14-poly) | 1+ | Irrigation supplier | [Irrigation Direct](https://www.irrigationdirect.ca/DD-DH250-100-1-4-x-100-Poly-Micro-Tubing-100-Roll-DD-DH250-100) |
| [Pressure regulator](#pressure-regulator) | 0-1 | Irrigation supplier | [Irrigation Direct](https://www.irrigationdirect.ca/dd-hpr10-drip-irrigation-pressure-regulator-10-psi-hose-threaded-3-4-c2c1-fht-x-3-4-mht.) |
| [Backflow preventer](#backflow-preventer) | 0-1 | Irrigation supplier | [Irrigation Direct](https://www.irrigationdirect.ca/dd-hvb-vacuum-breaker-3-4-hose-thread-anti-siphon-backflow-preventer-for-drip-irrigation.-c2c76) |
| [Vacuum relief valve](#vacuum-relief-valve) | 1 | Irrigation supplier | [Irrigation Direct](https://www.irrigationdirect.ca/dt-arv75-3-4-mpt-air-vacuum-relief-valve-c2f2) |
| [Filter](#filter) | 1 | Irrigation supplier | [Irrigation Direct](https://www.irrigationdirect.ca/Irritec-A4-HTF155-Drip-Irrigation-Y-Filter-3-4-Female-Hose-Swivel-x-Male-Hose-150-Stainless-Steel-Mesh-Screen) |

#### 1/2 Poly

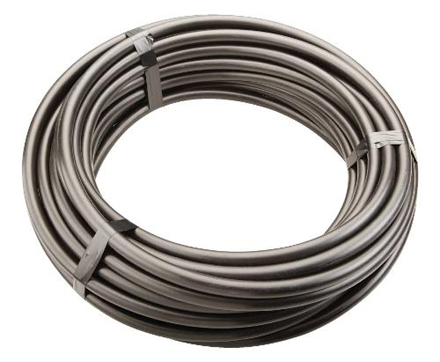
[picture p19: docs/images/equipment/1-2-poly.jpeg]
1/2 poly tubing


#### 1/4 Poly

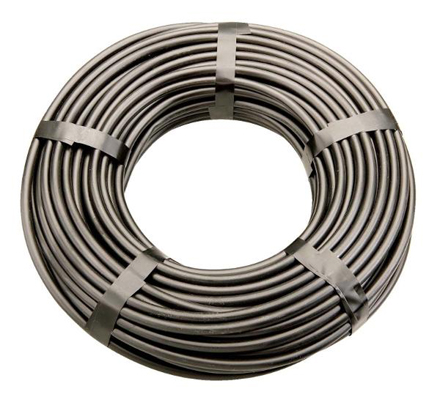
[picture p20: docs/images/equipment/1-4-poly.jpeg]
1/4 poly tubing


#### Pressure Regulator

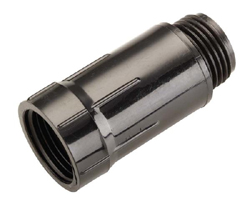
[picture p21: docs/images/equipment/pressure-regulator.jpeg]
10PSI pressure regulator


#### Backflow Preventer

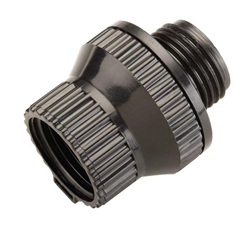
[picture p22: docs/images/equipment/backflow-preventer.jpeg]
Backflow preventer


#### Vacuum Relief Valve

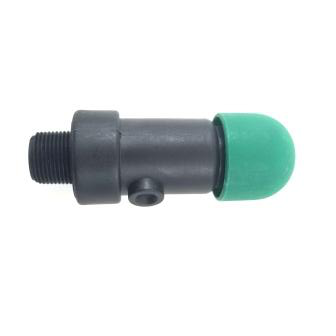
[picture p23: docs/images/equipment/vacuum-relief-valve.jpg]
Vacuum relief valve


#### Filter

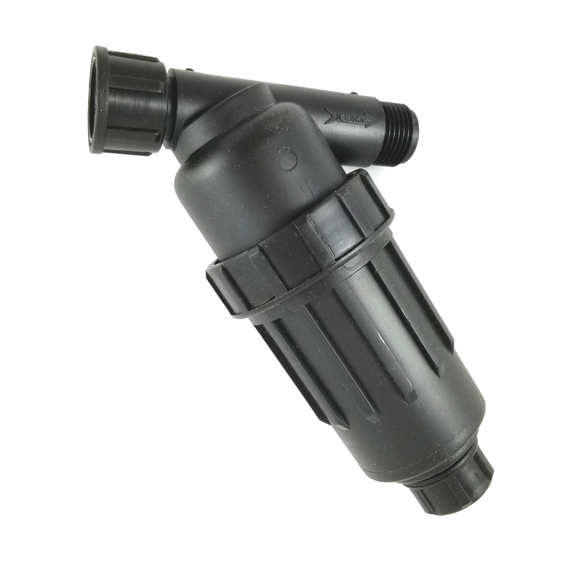
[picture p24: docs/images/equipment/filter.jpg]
Filter


### Fittings

These items are needed to fit together the fluids supplies.

| Item | Quantity | Where to source | Product Link |
| ---  | --- | --- | --- |
| [1/2 poly to 3/4 MHT](#12-poly-to-34-mht) | 1+ | Irrigation supplier | [Irrigation Direct](https://www.irrigationdirect.ca/dl-mh600-drip-irrigation-direct-loc-male-hose-end-.600-id-el-x-3-4-mht-700-or-710-tubing-b1b5) |
| [1/2 poly to 3/4 FHT](#12-poly-to-34-fht) | 1+ | Irrigation supplier | [Irrigation Direct](https://www.irrigationdirect.ca/DL-FHS600-Direct-Loc-Swivel-Adapter-.600-ID-DL-x-3-4-FHT-Swivel-700-or-710-Tubing.-DL-FHS600) |
| [1/2 poly to poly tee join](#12-poly-tee-join) | 0+ | Irrigation supplier | [Irrigation Direct](https://www.irrigationdirect.ca/DL-T600-Direct-Loc-Tee-.600-ID-700-or-710-Tubing.-DL-T600) |
| [1/2 poly elbow join](#12-poly-elbow-join) | 0+ | Irrigation supplier | [Irrigation Direct](https://www.irrigationdirect.ca/DL-L600-Direct-Loc-Elbow-.600-ID-DL-x-DL-700-or-710-Tubing.-DL-L600) |
| [Tank bulkhead](#tank-bulkhead) | 0-3 | 3D print | CAD folder |
| [Hose washer](#hose-washer) | 0-10 | Hardware store | [Home Depot](https://www.homedepot.ca/product/orbit-hose-washer-combo-12-pack-/1000474848) |
| [Tank bulkhead to 3/4 thread](#tank-bulkhead-to-34-thread) | 0-2 | 3D print | CAD folder |
| [Tank bulkhead to 1/4 poly](#tank-bulkhead-to-14-poly) | 0-1 | 3D print | CAD folder |
| [3/8 thread to 3/4 thread](#38-thread-to-34-thread) | 0-2 | 3D print | CAD folder |

#### 1/2 Poly to 3/4 MHT

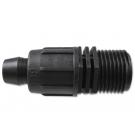
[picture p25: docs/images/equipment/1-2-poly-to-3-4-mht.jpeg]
1/2 poly tubing to 3/4 male hose thread


#### 1/2 Poly to 3/4 FHT

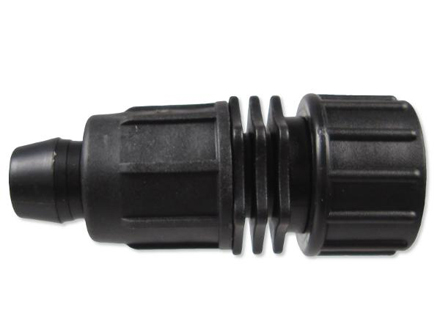
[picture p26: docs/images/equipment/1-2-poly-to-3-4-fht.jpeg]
1/2 poly tubing to 3/4 female hose thread


#### 1/2 Poly Tee Join

1/2 poly tubing 3-way tee join

#### 1/2 Poly Elbow Join

1/2 poly tubing elbow join

#### Tank Bulkhead

Tank bulkhead

#### Hose Washer

Hose washer

#### Tank Bulkhead to 3/4 Thread

Tank bulkhead to 3/4 inch thread

#### Tank Bulkhead to 1/4 Poly

Tank bulkhead to 1/4 inch poly

#### 3/8 Thread to 3/4 Thread

3/8 inch thread to 3/4 inch thread

### Irrigation System

These items are what I used to build out the rest of the irrigation system, after the section controlled by the irrigation controller. These items are going to be highly variable on the space the irrigation system is covering, and can be considered seperate from the system of the controller. I've just listed the items I used for reference.  

| Item | Quantity | Where to source | Product Link |
| ---  | --- | --- | --- |
| [Inline valve](#inline-valve) | 0+ | Irrigation supplier | [Irrigation Direct](https://www.irrigationdirect.ca/DL-FCV600-Pema-Loc-1-2-Flow-Control-Valve-DL-x-DL.-DL-FCV600) |
| [Tube cutter](#tube-cutter) | 1 | Irrigation supplier | [Irrigation Direct](https://www.irrigationdirect.ca/tl-tc100-3/4-tubing-cutter-b2e8) |
| [1/2 poly end](#12-poly-end) | 1+ | Irrigation supplier | [Irrigation Direct](https://www.irrigationdirect.ca/dd-f8-figure-8-end-of-line-plug.-b1c6) |
| [1/2 poly mount](#12-poly-mount) | 1+ | Irrigation supplier | [Irrigation Direct](https://www.irrigationdirect.ca/dd-mc700b-1-2-tubing-mounting-clamp-with-nail-black.-b2d2) |
| [Drip tape](#drip-tape) | 1+ | Irrigation supplier | [Irrigation Direct](https://www.irrigationdirect.ca/p1-1508-500-irritec-p1-drip-tape-15mil-x-8-spacing-.25-gpm-100ft) |
| [Drip tape barb](#drip-tape-barb) | 1+ | Irrigation supplier | [Irrigation Direct](https://www.irrigationdirect.ca/DT-TO250-Drip-Tape-5-8-Loc-x-1-4-Barb-DT-TO250) |
| [Drip tape hole punch](#drip-tape-hole-punch) | 1 | Irrigation supplier | [Irrigation Direct](https://www.irrigationdirect.ca/dd-hp250-dg-hole-punch-for-1-4-barbed-fittings-and-drippers-b2e3) |
| [Drip tape sleeve end](#drip-tape-sleeve-end) | 1+ | Irrigation supplier | [Irrigation Direct](https://www.irrigationdirect.ca/DT-TSE-Drip-Tape-5-8-Sleeve-End-DT-TSE.html) |
| [Drip tape stake](#drip-tape-stake) | 1+ | Irrigation supplier | [Irrigation Direct](https://www.irrigationdirect.ca/TLS6-Netafim-Drip-Tubing-Hold-Down-6-Wire-Stake-Staple-Style-fits-1-8-to-3-4-tubing-DD-S6.html) |

#### Inline Valve

Inline valve

#### Tube Cutter

Tube cutter

#### 1/2 Poly End

1/2 poly end

#### 1/2 Poly mount

1/2 poly mount

#### Drip Tape

5/8 Drip tape

#### Drip Tape Barb

Drip tape barb

#### Drip Tape Hole Punch

Drip tape hole punch

#### Drip Tape Sleeve End

Drip tape sleeve end

#### Drip Tape Stake

Drip tape stake

## Assembly

### Water Supplies

1. If [`USING_SOURCE_`](#auto-config), secure the use of a 3/4 inch threaded connection to a inexhaustible water supply, like a utility connection
2. If [`USING_TANK_`](#auto-config), secure a barrel or water storage container of some sort at a reasonably high location to generate water pressure for the whole system

### Devices

1. Solder a diode across each valve
2. Solder a connector to each valve
3. Screw each valve into a case
4. Solder a connector to the flow sensor
5. Screw flow sensor into case 
6. Solder a connector to the pressure sensor
7. Coat pressure sensor in water proof coating
8. Tightly insert pressure sensor port into case with some material like plumbers tape. Screw case closed

### Fluids

1. Attach a hose breaker to the source. Add a hose filter. Add a 3/4 thread to 1/2 poly adapter. Poly tube to the tank. 
2. Add 1/2 tube to 3/4 thread adapter, solenoid valve, and 3/4 thread adapter to 1/2 poly tube
3. Drill holes in the barrels x size. Insert the tank bulkheads into them with one hose washer on each side. Screw tightly
4. To the output hole, add a tank bulkhead to 3/4 thread adapter, then a no minimum pressure solenoid valve, a 3/4 thread to 1/2 poly adapter
5. Add whatever turns you need to get the source valve and tank valve to meet. Then join them with a tee
6. Add the filter, then the vacuum relief valve. then the flow sensor. Then extend the line to a point of entry into the system
7. To the drain hole, add a tank bulkhead to 3/4 thread adapter, then a no minimum pressure solenoid valve, a 3/4 thread to 1/2 poly adapter.
8. To the overflow hole, add a tank bulkhead to 3/4 thread adapter, then a poly section that connects with the drain valve and goes to the bypass storm drain
9. Screw on the 1/4 poly to tank bulkhead attachment, and extend a support section out to wherever the pressure hole is. Screw on the pressure sensor at the right angle to minimize the amount of tube used. Join with 1/4 poly

### Electrical

0. Flash ESP
1. Solder pins onto esp8266, voltage regulator, and logic level converter
2. Solder components onto board
3. Add wires onto power supply adapter and solder them into voltage regulator as wel as connected into relaty. Add adapter into case
4. Connect regulator to power line and those to all other components
5. Connect esp to relay
6. Pre-solder connections for all other pins
7. Screw board and relay into case.
8. Place the controller case where it will be relative to the devices
9. Size wire length to each device. Cut wires and solder on connectors
10. Insert wires into controller case and connect to the board and relay
11. Cut out plastic insulators for the top of the controller case and screw on.

### Calibration

1. Send a message to the calibration start topic
2. Prepare a fluid measuring device and send amount of time to the calibration listed topic
3. Send the measured amount of fluid to the calibration set topic
4. Repeat until enough samples and send a message to the calibration start topic again with the id to stop the process

### Irrigation System

1. To the rain water input hole, add a tank bulkhead to 3/4 thread and a 3/4 thread to 1/2 poly
2. Connect the input to the rain somehow
3. Build up rest of irrigation system with chosen materials

# Software configuration

## Configuration

All configuration settings can be found in the file `config.h`. **Assume that all settings require your attention unless otherwise stated.**

### Core

These settings define the [operating mode](#operating-modes) of the device. Make sure you have the correct hardware connected before you enable any related settings here.

- `DEBUG bool` Defines whether to output debugging info to the serial log.

- `RESEVOIR_MODE int` Defines which [types of water supplies](#water-supplies) the controller is connected to.
    - `1` Source
    - `2` Tank
    - `3` Both

- `USING_SOURCE_FLOW bool` If using a source, define the method of flow rate estimation. 
    - `true` A flow sensor measures the flow rate. This is useful if the source has a variable flow, or if a tank (and thus flow sensor) is already being used.
    - `false` A flow sensor is not being used. A static flow rate for the source must be configured through [`SourceConfig.static_flow_rate`](#runtime-config). 

-  `USING_DRAIN_VALVE bool` If using a tank, define whether the controller is connected to a drain valve on the tank.
    - `true`
    - `false`

- `USING_PRESSURE_SENSOR bool` If using a tank, define whether the controller is connected to a pressure sensor measuring the absolute pressure at the bottom of the tank.
    - `true`
    - `false`

### WiFi Manager

These settings are used to configure the WiFi Manager, an instance of the WiFiManager class (see [dependencies](#dependencies)). This class enables the configuration of the WiFi network and MQTT broker through an access point hosted by the controller, rather than being hard coded into the software.

- `AP_NAME string` The SSID of the auto-connect access point.

- `AP_PASSWORD string` The password of the auto-connect access point.

- `AP_IP IPAddress()` The IP address of the auto-connect access point. **You should ensure this doesn't conflict with another device on your network, but otherwise doesn't need to be changed.**

- `AP_GATEWAY IPAddress()` The gateway of the auto-connect access point. **This likely does not need to be changed.**

- `AP_SUBNET IPAddress()` The subnet of the auto-connect access point. **This likely does not need to be changed.**

- `AP_TIMEOUT int` The duration of time the auto-connect access point is kept open in seconds. **This likely does not need to be changed.**

- `AP_RETRY_DELAY int` The duration of time to wait between auto-connect access point timeout and next try in seconds. **This likely does not need to be changed.**

- `AP_RETRY_DEEP_SLEEP bool` Define the method used to wait for `AP_RETRY_DELAY`.
    - `true` The ESP8266 function `ESP.deepSleep()` will be used to reduce power consumption. See the [electrical assembly](#electrical) section for the required electrical wiring.
    - `false` The Arduino function `delay()` followed by `ESP.restart()` will be used.

### MQTT

These settings are used to configue the MQTT client, an instance of the PubSubClient class(see [dependencies](#dependencies)). This class enables interaction with an MQTT broker. The settings marked as `DEFAULT` are able to be configured through the WiFi Manager access point.

- `MQTT_SERVER_DOMAIN_DEFAULT string` The domain, or URL, of the MQTT broker to connect to.

- `MQTT_SERVER_PORT_DEFAULT string` The port on the MQTT broker to connect to.

- `MQTT_ID_DEFAULT string` The ID of the client.

- `MQTT_USE_CREDENTIALS bool` Whether to connect to the MQTT broker using a username and password. If false, username and password will still show up on the auto-connect access point, but they can be safely ignored as they won't be used to make the connection. 

- `MQTT_USERNAME_DEFAULT string` The username of the client.

- `MQTT_PASSWORD_DEFAULT string` The password of the client.

- `MQTT_RETRY_TIMEOUT int` The duration of time to continually attempt connection to the MQTT broker before returning to the auto-connect access point, in seconds. **This likely does not need to be changed.**

- `MQTT_MAX_BUFFER_SIZE int` The maximum message size of an MQTT message, in bytes. **This likely does not need to be changed. Be aware of perfomance impacts when adjusting outsize the range of 256-512 bytes.**

- `MQTT_KEEPALIVE int` The keepalive interval, in seconds.

### Pins

These settings define the pins used to interact with the equipment connected to the controller. Don't worry about changing the settings that don't apply to your use case - unused pins are automatically set to -1 in the [auto-config](#auto-config). 

- `SOURCE_OUTPUT_VALVE_PIN int` The output pin connected to the source output valve. High signals should open the valve.

- `TANK_OUTPUT_VALVE_PIN int` The output pin connected to the tank output valve. High signals should open the valve.

- `TANK_DRAIN_VALVE_PIN int` The output pin connected to the tank drain valve. High signals should open the valve.

- `FLOW_SENSOR_PIN int` The input pin connected to the flow sensor data wire. See the [equipment](#flow-sensor) section to ensure compatible logic levels and interrupt-capability.

### Defaults

These settings are default settings that can be changed at runtime through the [config change topic](#write), where they are written to a file on the controller's file system memory and stored in [config structs](#runtime-config). Sensible defaults should still be set here to avoid having to manually update each setting.  

- `DATA_RESOLUTION_L_DEFAULT float` The default value of [`ServicesConfig.data_resolution_l`](#runtime-config). **This likely does not need to be changed.**

- `STATIC_FLOW_RATE_DEFAULT float` The default value of [`SourceConfig.static_flow_rate`](#runtime-config).

- `PULSES_PER_L_DEFAULT float` The default value of [`FlowSensorConfig.pulses_per_l`](#runtime-config).

- `MAX_FLOW_RATE_DEFAULT float` The default value of [`FlowSensorConfig.max_flow_rate`](#runtime-config).

- `MIN_FLOW_RATE_DEFAULT float` The default value of [`FlowSensorConfig.min_flow_rate`](#runtime-config).

- `FLOW_CALIBRATION_TIMEOUT int` The default value of [`FlowSensorConfig.calibration_timeout`](#runtime-config). **This does not need to be changed.**

- `FLOW_CALIBRATION_MAX_VOLUME float` The default value of [`FlowSensorConfig.calibration_max_volume`](#runtime-config). **This does not need to be changed.**

- `TANK_TIMEOUT_DEFAULT int` The default value of [`TankConfig.tank_timeout`](#runtime-config). **This does not need to be changed.**

- `TANK_SHAPE_DEFAULT int` The default value of [`TankConfig.shape_type`](#runtime-config).

- `TANK_DIMENSION_1_DEFAULT float` The default value of [`TankConfig.dimension_1`](#runtime-config).

- `TANK_DIMENSION_2_DEFAULT float` The default value of [`TankConfig.dimension_2`](#runtime-config).

- `TANK_DIMENSION_3_DEFAULT float` The default value of [`TankConfig.dimension_3`](#runtime-config).

- `PRESSURE_REPORT_MODE_DEFAULT int` The default value of [`PressureSensorConfig.report_mode`](#runtime-config). **This does not need to be changed.**

- `ATMOSPHERIC_PRESSURE_HPA_DEFAULT float` The default value of [`PressureSensorConfig.atmosphere_pressure`](#runtime-config). **This does not need to be changed. Unless you live on Mount Everest, or Mars or something like that.**

### Runtime Config

These settings are initialized at runtime, first reading a configuration file from the file system, then using and writing to the file the [default values](#defaults) if the file doesn't exist. The file can be update at runtime through the [config write](#write) topic. 

- `ServicesConfig.data_resolution_l = float` The volume interval at which slice reports are sent to the [dispense slice report](#slice-reporting) topic during the dispense process, in liters. 

- `SourceConfig.static_flow_rate = float` The static flow rate to use for the source output volume in liters. Enabled if [`USING_SOURCE_FLOW`](#core) is false.

- `TankConfig.tank_timeout = int` The delay in seconds between the start of a dispense process and the first moment a flow rate lower than `FlowSensorConfig.min_flow_rate` can result in either the dispense process ending or switching to the source, depending on the value of [`USING_SOURCE_`](#auto-config).

- `TankConfig.shape_type = int` The geometric shape of the tank, used in the conversion from tank pressure to volume. This conversion is done with a function called `pressure_to_volume()` in the file `app.cpp`.
    - `1` The tank is a rectangular prism. `TankConfig.dimension_1` describes length, `TankConfig.dimension_2` describes width, and `TankConfig.dimension_3` describes height.
    - `2` The tank is a cylinder. `TankConfig.dimension_1` describes diameter, `TankConfig.dimension_2` describes height, and `TankConfig.dimension_3` is unused.

- `TankConfig.dimension_1 = float` The first dimension of the tank's geometry, depending on `TankConfig.shape_type`.

- `TankConfig.dimension_2 = float` The second dimension of the tank's geometry, depending on `TankConfig.shape_type`.

- `TankConfig.dimension_3 = float` The third dimension of the tank's geometry, depending on `TankConfig.shape_type`.

- `FlowSensorConfig.pulses_per_l = float` Defines the amount of pulses returned by the flow sensor per liter.

- `FlowSensorConfig.max_flow_rate = float` Defines the maximum rated flow rate of the flow sensor in liters per minute. When the dispense flow rate surpasses this value, a warning will be sent to [`WARNING_TOPIC_`](#auto-config).

- `FlowSensorConfig.min_flow_rate = float` Defines the minimum rated flow rate of the flow sensor in liters per minute. When the dispense flow rate goes below this value, a warning will be sent to [`WARNING_TOPIC_`](#auto-config). If the active water supply is the tank, a flow rate below this value, combined with a current dispense duration greater than `TankConfig.tank_timeout`, will result in the dispense either shutting off or switching to the source, depending on [`USING_SOURCE_`](#auto-config).

- `FlowSensorConfig.calibration_timeout = int` Defines the duration of time, in seconds, after which the flow sensor calibration process will be ended if no dispense requests or measurments are made.

- `FlowSensorConfig.calibration_max_volume = float` Defines the maximum volume, in liters, to allow to be dispensed at a time during the flow sensor calibration process. 

- `PressureSensorConfig.report_mode = int` When reporting values related the pressure in the tank, define which values to report.
    - `1` Pressure in hectopascals.
    - `2` Volume in liters. Requires the tank geometry is correctly configured.
    - `3` Both.

- `PressureSensorConfig.atmosphere_pressure = float` The pressure in hectopascals to be subtracted from the absolute pressure returned by the pressure sensor, in order to find the gauge pressure in the tank.

### Topics

These settings define the topic strings to use for the MQTT interface. See the [MQTT interface](#mqtt-interface) for details.

**You can leave these unchanged with no problem,** but you might want to customize them. If you do, just keep in mind that the topic strings are sent with every message, and that the MQTT client has a maximum message size of 256 bytes (including header). Try to keep them small, especially for topics with a high message frequency (like [`DISPENSE_REPORT_SLICE_TOPIC_`](#auto-config)), or a large payload (like [`CONFIG_TOPIC_`](#auto-config)). 

- `BASE_TOPIC string` The base topic used to pre-pend all other topics through the [auto-config](#auto-config).

- `DISPENSE_ACTIVATE_TOPIC string` The topic used to recieve [dispense activation](#activation) requests.

- `DISPENSE_REPORT_SLICE_TOPIC string` The topic used to send [dispense slice reports](#slice-reporting).

- `DISPENSE_REPORT_SUMMARY_TOPIC string` The topic used to send [dispense summary reports](#summary-reporting).

- `DEACTIVATE_TOPIC string` The topic used to recieve [deactivation requests](#deactivation).

- `RESTART_TOPIC string` The topic used to recieve [restart requests](#restart).

- `LOG_TOPIC string` The topic used to send [info logs](#info).

- `WARNING_TOPIC string` The topic used to send [warning logs](#warnings).

- `ERROR_TOPIC string` The topic used to send [error logs](#errors).

- `CONFIG_TOPIC string` The topic used to send current [config values](#read) in a retained message.

- `AUTO_CONFIG_TOPIC_` The topic used to send [auto-config values]() in a retained message.

- `TOPIC_CONFIG_TOPIC_` The topic used to send [topic string values]() in a retained message.

- `CONFIG_CHANGE_TOPIC string` The topic used to recieve [config change requests](#write).

- `SETTINGS_RESET_TOPIC string` The topic used to recieve [settings reset requests](#reset-settings).

- `FLOW_SENSOR_CALIBRATE_BEGIN_TOPIC string` The topic used to [begin flow sensor calibration](#flow-sensor-calibration) requests.

- `FLOW_SENSOR_CALIBRATE_DISPENSE_TOPIC string` The topic used to recieve [flow sensor calibration dispense](#dispense) requests.

- `FLOW_SENSOR_CALIBRATE_MEASURE_TOPIC string` The topic used to recieve [flow sensor calibration measurments](#measure).

- `DRAIN_ACTIVATE_TOPIC string` The topic used to recieve [drain activation](#activation-1) requests.

- `DRAIN_REPORT_SUMMARY_TOPIC string` The topic used to send [drain summary reports](#summary-reporting-1).

- `PRESSURE_REQUEST_TOPIC string` The topic used to [request pressure reports](#request).

- `PRESSURE_REPORT_TOPIC string` The topic used to [send pressure reports](#report).

### Auto-Config

These settings are configured automatically and shouldn't be altered unless you're willing to change other parts of the code. They're self explanatory, but listed here for reference.

```
// ************* Operating mode ************* //
#define USING_SOURCE_ ((RESEVOIR_MODE == 1 || RESEVOIR_MODE == 3) ? true : false)
#define USING_TANK_ ((RESEVOIR_MODE == 2 || RESEVOIR_MODE == 3) ? true : false)
#define USING_DRAIN_VALVE_ ((USING_TANK_ && USING_DRAIN_VALVE) ? true : false)
#define USING_FLOW_SENSOR_ ((USING_TANK_ || USING_SOURCE_FLOW) ? true : false)
#define USING_PRESSURE_SENSOR_ ((USING_TANK_ && USING_PRESSURE_SENSOR) ? true : false)

// ************* Pins ************* //
// Define pins to -1 to indicate non-use based on operational mode
#define SOURCE_OUTPUT_VALVE_PIN_ (USING_SOURCE_ ? SOURCE_OUTPUT_VALVE_PIN : -1)
#define TANK_OUTPUT_VALVE_PIN_ (USING_TANK_ ? TANK_OUTPUT_VALVE_PIN : -1)
#define TANK_DRAIN_VALVE_PIN_ (USING_DRAIN_VALVE_ ? TANK_DRAIN_VALVE_PIN : -1)
#define FLOW_SENSOR_PIN_ (USING_FLOW_SENSOR_ ? FLOW_SENSOR_PIN : -1)

// ************* MQTT topics ************* //
// Define topics to NULL to indicate non-use based on operational mode
#define DISPENSE_ACTIVATE_TOPIC_ (BASE_TOPIC DISPENSE_ACTIVATE_TOPIC)
#define DISPENSE_REPORT_SLICE_TOPIC_ (BASE_TOPIC DISPENSE_REPORT_SLICE_TOPIC)
#define DISPENSE_REPORT_SUMMARY_TOPIC_ (BASE_TOPIC DISPENSE_REPORT_SUMMARY_TOPIC)
#define DEACTIVATE_TOPIC_ (BASE_TOPIC DEACTIVATE_TOPIC)
#define RESTART_TOPIC_ (BASE_TOPIC RESTART_TOPIC)
#define LOG_TOPIC_ (BASE_TOPIC LOG_TOPIC)
#define WARNING_TOPIC_ (BASE_TOPIC WARNING_TOPIC)
#define ERROR_TOPIC_ (BASE_TOPIC ERROR_TOPIC)
#define CONFIG_TOPIC_ (BASE_TOPIC CONFIG_TOPIC)
#define TOPIC_CONFIG_TOPIC_ (BASE_TOPIC TOPIC_CONFIG_TOPIC)
#define CONFIG_CHANGE_TOPIC_ (BASE_TOPIC CONFIG_CHANGE_TOPIC)
#define CONFIG_CHANGE_TOPIC_ (BASE_TOPIC CONFIG_CHANGE_TOPIC)
#define SETTINGS_RESET_TOPIC_ (BASE_TOPIC SETTINGS_RESET_TOPIC)
#define FLOW_SENSOR_CALIBRATE_BEGIN_TOPIC_ (USING_FLOW_SENSOR_ ? (BASE_TOPIC FLOW_SENSOR_CALIBRATE_BEGIN_TOPIC) : NULL)
#define FLOW_SENSOR_CALIBRATE_DISPENSE_TOPIC_ (USING_FLOW_SENSOR_ ? (BASE_TOPIC FLOW_SENSOR_CALIBRATE_DISPENSE_TOPIC) : NULL)
#define FLOW_SENSOR_CALIBRATE_MEASURE_TOPIC_ (USING_FLOW_SENSOR_ ? (BASE_TOPIC FLOW_SENSOR_CALIBRATE_MEASURE_TOPIC) : NULL)
#define DRAIN_ACTIVATE_TOPIC_ (USING_DRAIN_VALVE_ ? (BASE_TOPIC DRAIN_ACTIVATE_TOPIC) : NULL)
#define DRAIN_REPORT_SUMMARY_TOPIC_ (USING_DRAIN_VALVE_ ? (BASE_TOPIC DRAIN_REPORT_SUMMARY_TOPIC) : NULL)
#define PRESSURE_REQUEST_TOPIC_ (USING_PRESSURE_SENSOR_ ? (BASE_TOPIC PRESSURE_REQUEST_TOPIC) : NULL)
#define PRESSURE_REPORT_TOPIC_ (USING_PRESSURE_SENSOR_ ? (BASE_TOPIC PRESSURE_REPORT_TOPIC) : NULL)
```

## Dependencies

WiFi manager: https://github.com/tzapu/WiFiManager Version: 2.0.15-rc.1
https://pubsubclient.knolleary.net/ Version: 2.8.0
https://arduinojson.org/ Version: 6.21.0

https://github.com/adafruit/Adafruit_Sensor Version 1.1.8 (For MPRLS library)
https://github.com/adafruit/Adafruit_BusIO Version 1.14.0 (For MPRLS library)
https://github.com/adafruit/Adafruit_MPRLS Version 1.1.0 (For pressure sensor)

## For Contributors

### Explanation of the purposes of different files

### Explanation of app state 

### Explanation of future plans for interface through verdantech web

# Bug reporting and contributing

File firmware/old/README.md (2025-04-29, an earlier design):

# Firmware Design

The firmware is currently being defined in header files, with most implementation code still blank.

The firmware uses a design with the following properties:

- It is centered around a finite state machine manager which runs in a main application task, with other tasks being used for background tasks such as filling queues of incoming data.
- Application logic is contained in Manager classes, with managers having only one-way interdepency between them.
- Manager classes may initialize Driver classes to further abstract low-level driver code.

The application code is contained in the `components` folder with the following components:

- `adc` contains drivers for the ADC.
- `config` contains the configuration data structures and persistence mechanism.
- `connection` is responsible for establishing a WiFi and MQTT connection.
- `errors` is for defining app errors.
- `flow` is responsible for reading data from the flow meter and executing the calibration process.
- `fsm` contains the state manager and all main application routine logic.
- `gpio` contains handles to the GPIO pins.
- `mqtt` is responsible for receiving and transmitting MQTT messages.
- `pressure` is responsible for reading data from the pressure sensor and executing the calibration process.
- `valves` is responsible for managing the dispense and drain processes.

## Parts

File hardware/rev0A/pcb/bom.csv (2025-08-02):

Reference | Value | Footprint | Description | Qty | LCSC Part | JLC | DNP
F1 | 330uH | easyeda2kicad:IND-SMD_L12.3-W12.3 | Inductor | 1 | 10152
R3,R4,R6,R8,R10,R11,R12,R13,R14,R15 | 10000 | easyeda2kicad:R1206 | Resistor | 10 | C1489
C8,C12,C13,C14,C15,C16,C18 | 0.1uF | easyeda2kicad:C0402 | Unpolarized capacitor | 7 | C1525
C3,C4,C6,C9 | 1uF | easyeda2kicad:C0603 | Unpolarized capacitor | 4 | C1592
C10,C11 | 22pF | easyeda2kicad:C0603 | Unpolarized capacitor | 2 | C1653
C5,C7,C17 | 10uF | easyeda2kicad:C0805 | Unpolarized capacitor | 3 | C1713
D8,D9,D10,D11,D12,D13 | 1N4148W | easyeda2kicad:SOD-123_L2.8-W1.8-LS3.7-RD | 75V 0.15A Fast Switching Diode, SOD-123 | 6 | C2099
D3 | 1N5822 | easyeda2kicad:DO-201AD_BD5.3-L8.4-P12.50-D1.4-FD | 40V 3A Schottky Barrier Rectifier Diode, DO-201AD | 1 | C2476
C1 | 100uF | easyeda2kicad:CAP-SMD_BD8.0-L8.3-W8.3-FD | Polarized capacitor | 1 | C3352
U1 | LM2575T-5.0 | easyeda2kicad:TO-263-5_L10.2-W8.9-P1.70-TL | Fixed 5.0V 52kHz Simple 1A Buck Regulator, TO-220-5 | 1 | C12061
F1 | 1A | easyeda2kicad:F1812 | Fuse | 1 | C17313
R5,R7,R9 | 1000 | easyeda2kicad:R0603 | Resistor | 3 | C21190
R1,R2 | 5100 | easyeda2kicad:R0603 | Resistor | 2 | C23186
K1,K2,K3 | SRD-12VDC-SL-C | easyeda2kicad:RELAY-TH_SRD-XXVDC-XL-C |  | 3 | C30431
U5 | TXS0102DCU | Package_SO:VSSOP-8_2.3x2mm_P0.5mm | 2-Bit Bidirectional Voltage-Level Shifter for Open-Drain and Push-Pull Application, VSSOP-8 | 1 | C53434
J7 | 3 Pin JST | easyeda2kicad:CONN-TH_3P-P2.50_A2501WV2-3P | Generic connector, single row, 01x03, script generated (kicad-library-utils/schlib/autogen/connector/) | 1 | C144394
J4,J5,J6,J8 | 2 Pin JST | easyeda2kicad:CONN-TH_B2B-XH-A-LF-SN | Generic connector, single row, 01x02, script generated (kicad-library-utils/schlib/autogen/connector/) | 4 | C158012
J2 | TYPE-C-31-M-12 | easyeda2kicad:USB-C_SMD-TYPE-C-31-M-12 |  | 1 | C165948
R16 | 120 | easyeda2kicad:RES-TH_BD2.2-L6.5-P10.50-D0.6 | Resistor | 1 | C172969
Q1,Q2,Q3 | BC337 | easyeda2kicad:TO-92-3_L4.8-W3.7-P2.54-R | 0.8A Ic, 45V Vce, NPN Transistor, TO-92 | 3 | C328602
D1,D4,D5,D6 | LESD5D5.0CT1G | easyeda2kicad:SOD-523_L1.2-W0.8-LS1.6-BI |  | 4 | C383211
U3 | LDL1117S33R | easyeda2kicad:SOT-223-4_L6.5-W3.5-P2.30-LS7.0-BR |  | 1 | C435835
U6 | ADS1115IRUGT | easyeda2kicad:X2QFN-10_L2.0-W1.5-P0.50-TL_RUG0010B |  | 1 | C701611
U2 | TPS22919QDCKRQ1 | easyeda2kicad:SC-70-6_L2.0-W1.3-P0.65-LS2.1-BR |  | 1 | C2871558
C2 | 330uF | easyeda2kicad:CAP-SMD_BD10.0-L10.3-W10.3-LS11.3-FD | Polarized capacitor | 1 | C2895745
U4 | ESP32-C3-WROOM-02-H4 | RF_Module:ESP32-C3-WROOM-02 | 802.11 b/g/n Wi-Fi and Bluetooth 5 module, ESP32-C3 SoC, RISC-V microprocessor, On-board antenna | 1 | C2944070
J1 | EJ508A | easyeda2kicad:DC-IN-TH_EJ508A | DC Barrel Jack with an internal switch | 1 | C3030986
D2,D7 | MBR230LSFT1G | easyeda2kicad:SOD-123FL_L2.8-W1.8-LS3.6-RD | 40V 1A Schottky Barrier Rectifier Diode, DO-41,Schottky diode | 2 | C5377812
J3 | 6 Pin Socket Header | easyeda2kicad:HDR-TH_6P-P2.54-V-F | Generic connector, single row, 01x06, script generated (kicad-library-utils/schlib/autogen/connector/) | 1 | C41413860
SW1,SW2 | SW_Push | easyeda2kicad:SW-TH_4P-L6.0-W6.0-P4.50-LS6.5 | Push button switch, generic, two pins | 2 | C42416249

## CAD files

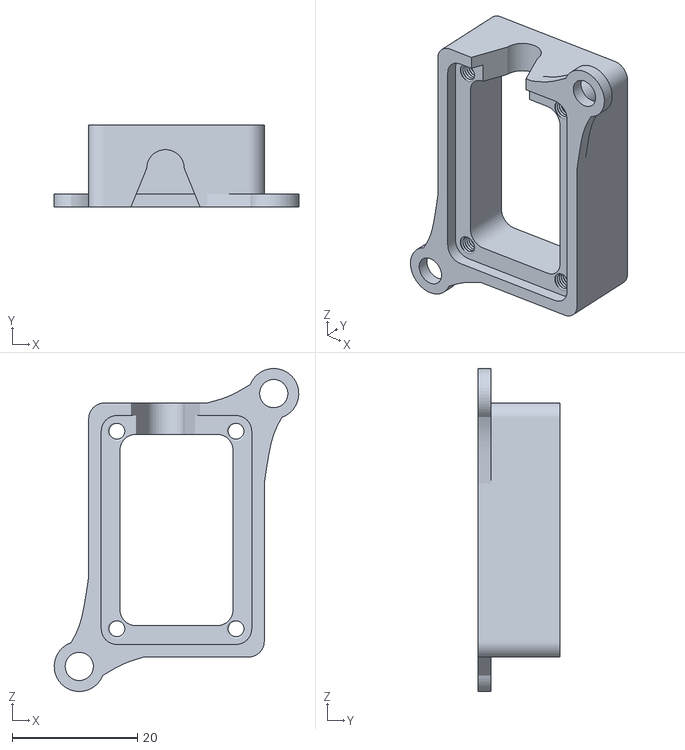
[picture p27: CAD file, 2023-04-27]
hardware/models/pressure case middle.stl
39.0 x 13.0 x 51.5

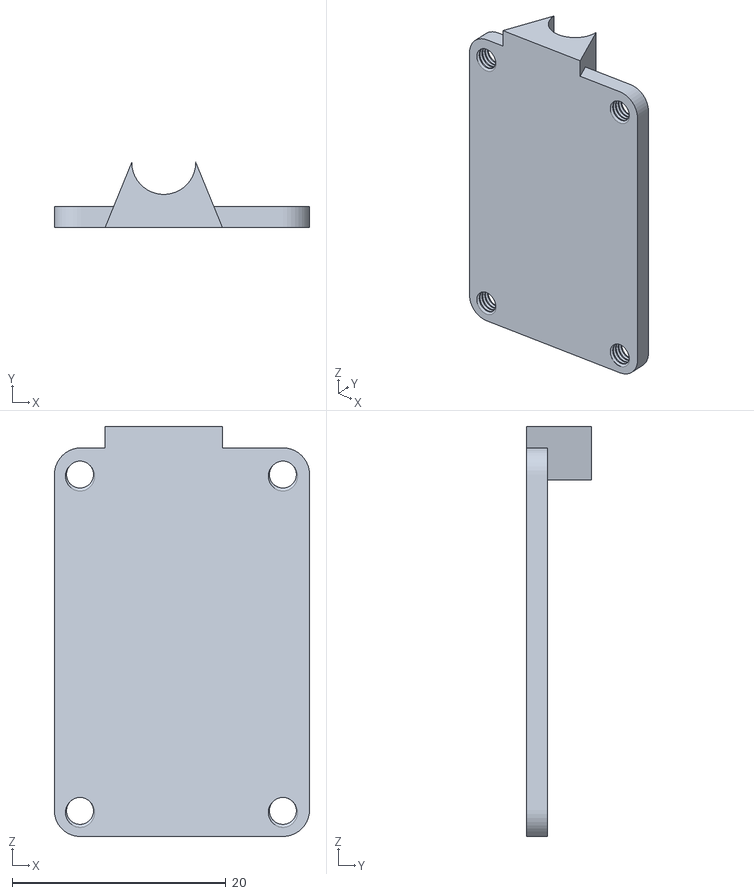
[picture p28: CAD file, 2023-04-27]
hardware/models/pressure case bottom.stl
23.9 x 6.11 x 38.4

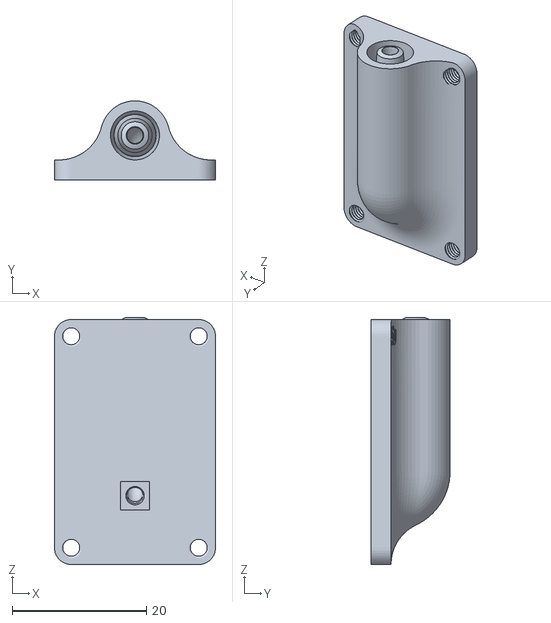
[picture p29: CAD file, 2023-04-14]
hardware/models/pressure case top.stl
24.0 x 11.8 x 36.8

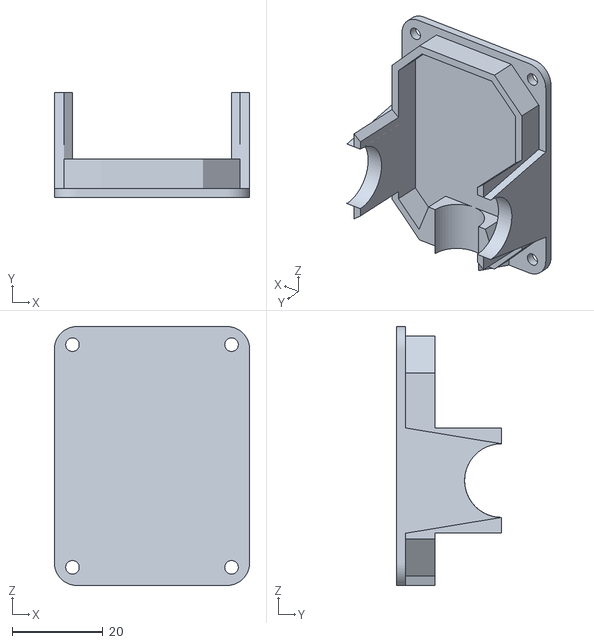
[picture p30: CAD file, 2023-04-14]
hardware/models/flow sensor case top.stl
43.0 x 23.1 x 57.0

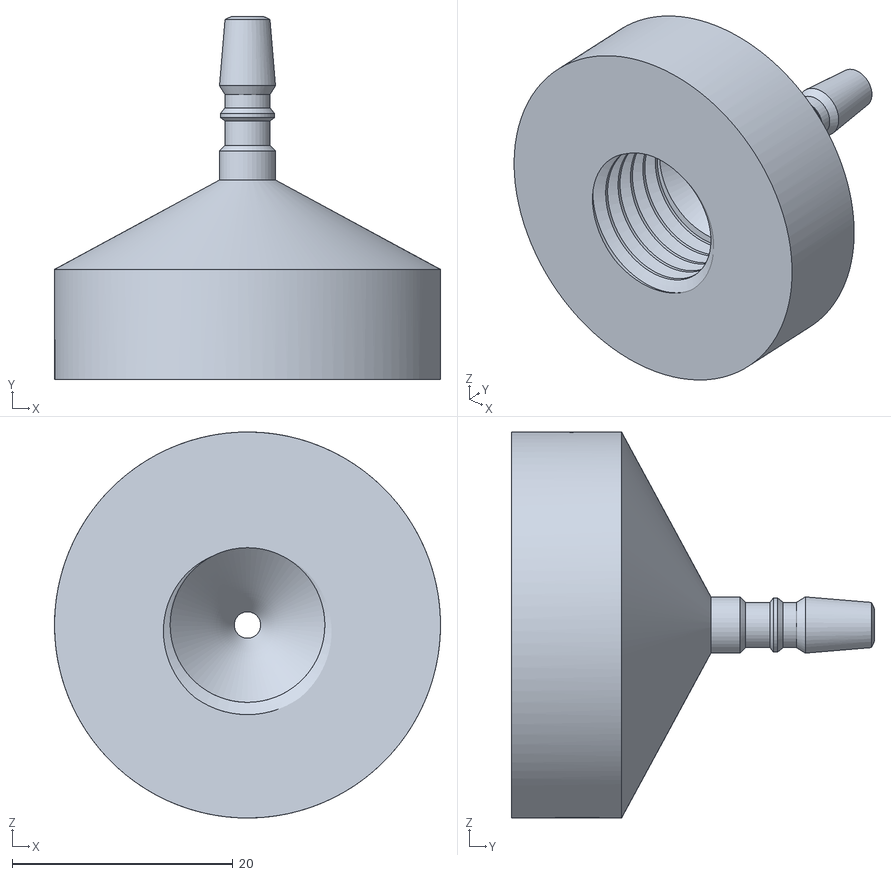
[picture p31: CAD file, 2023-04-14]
hardware/models/bulkhead to 1-4 poly.stl
35.0 x 33.0 x 35.0

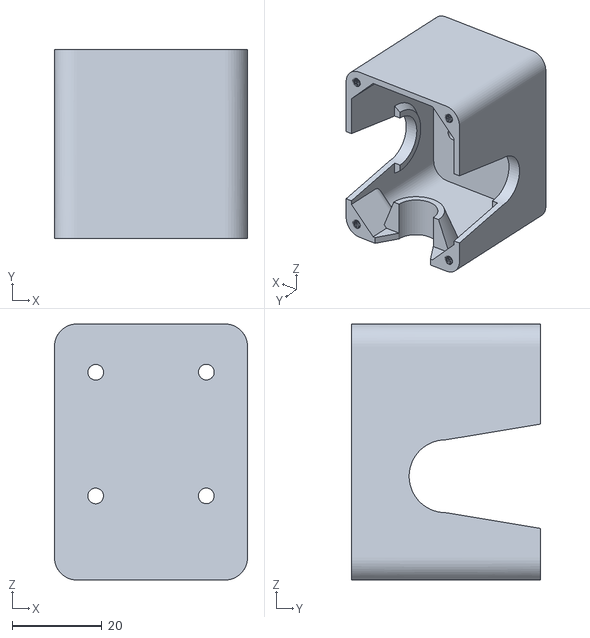
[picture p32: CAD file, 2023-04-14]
hardware/models/flow sensor case bottom.stl
43.0 x 42.0 x 57.0

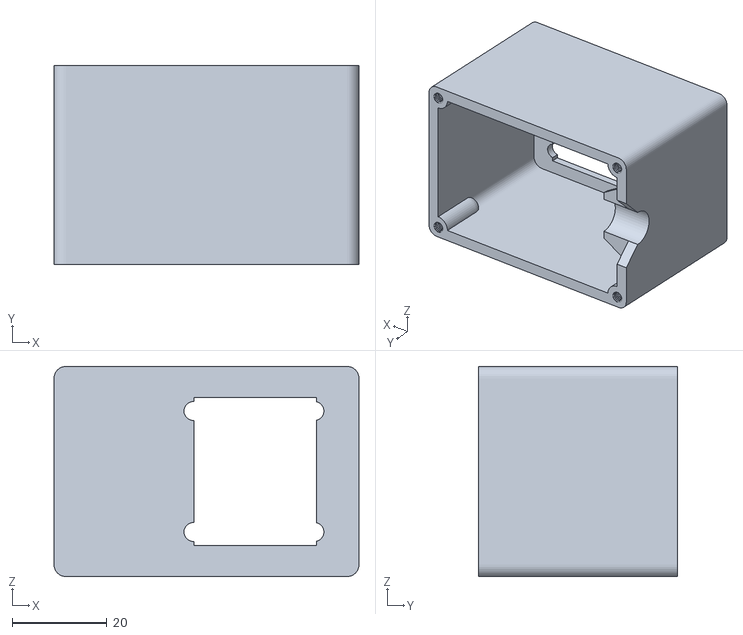
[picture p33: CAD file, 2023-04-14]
hardware/models/valve case bottom.stl
64.3 x 42.0 x 44.3

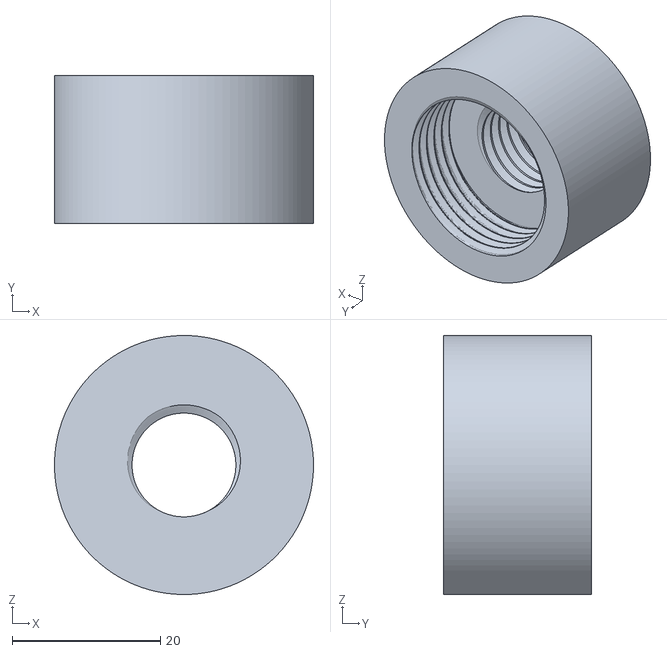
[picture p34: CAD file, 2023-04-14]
hardware/models/bulkhead to 3-4 MHT.stl
35.0 x 20.0 x 35.0

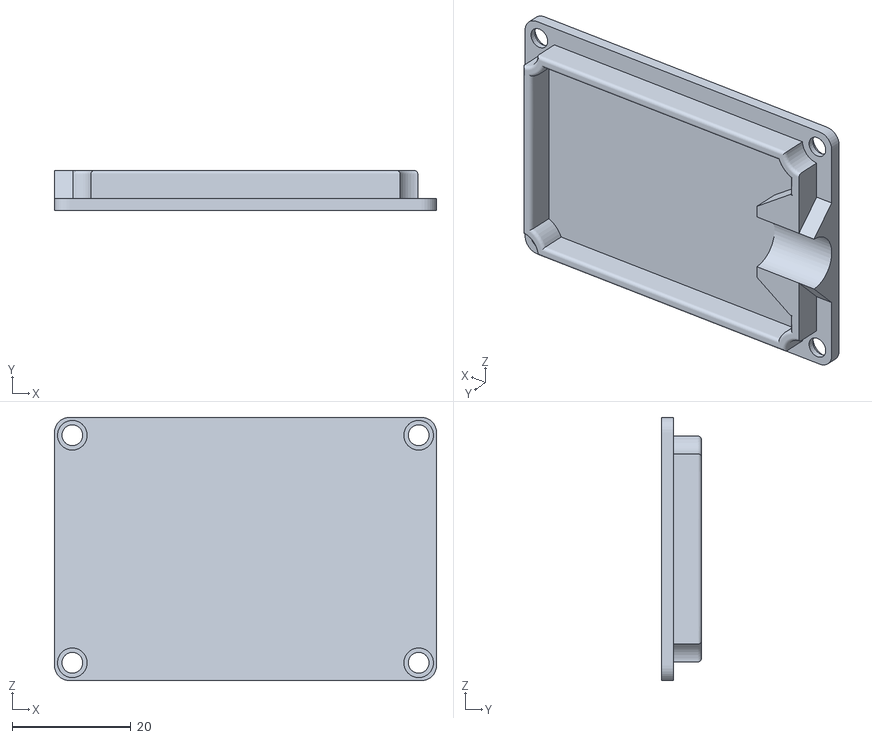
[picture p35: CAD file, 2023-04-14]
hardware/models/valve case top.stl
64.3 x 6.75 x 44.3

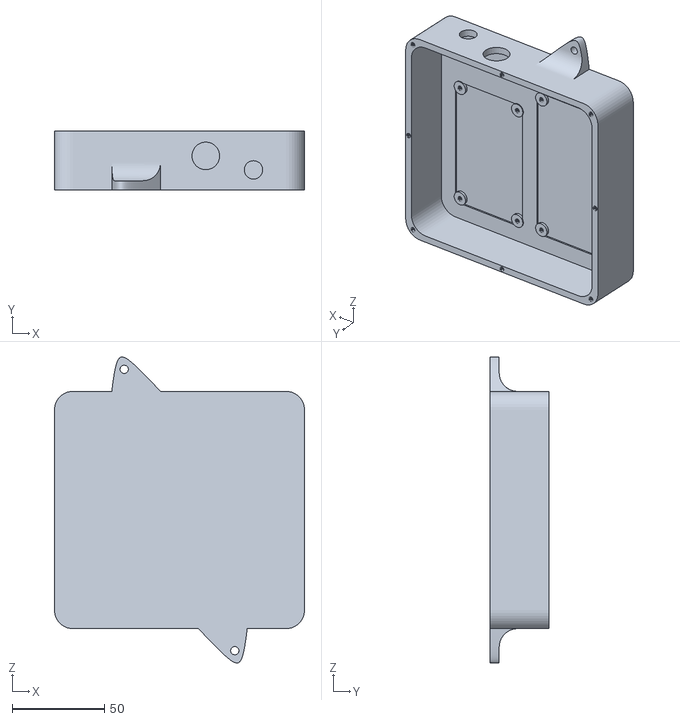
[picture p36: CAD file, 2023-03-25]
hardware/models/controller case bottom.stl
135.7 x 32.0 x 166.1

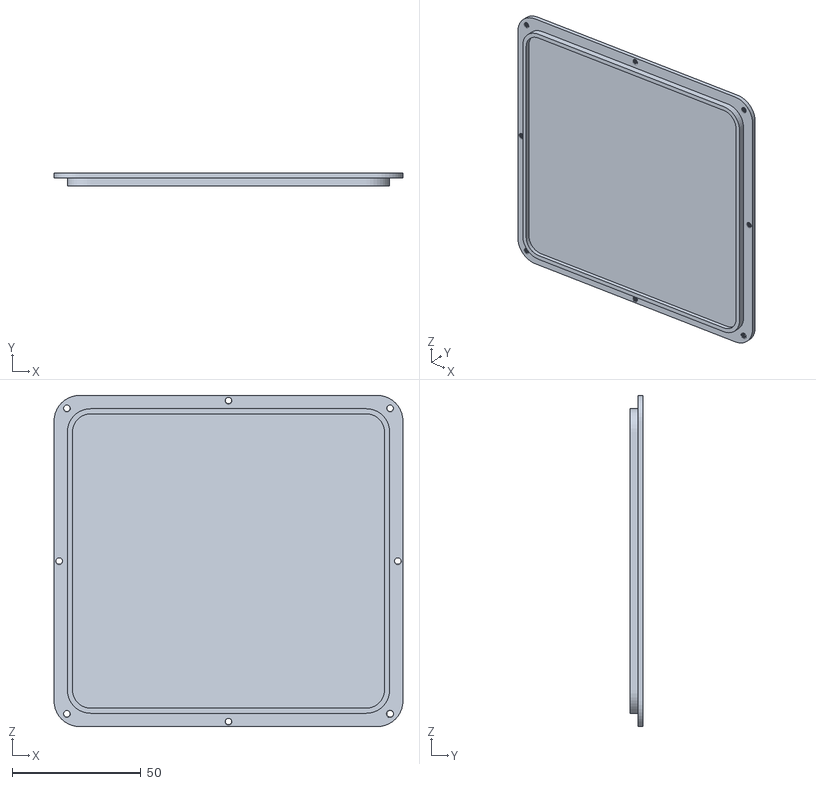
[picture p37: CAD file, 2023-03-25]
hardware/models/controller case top.stl
135.7 x 5.00 x 128.8

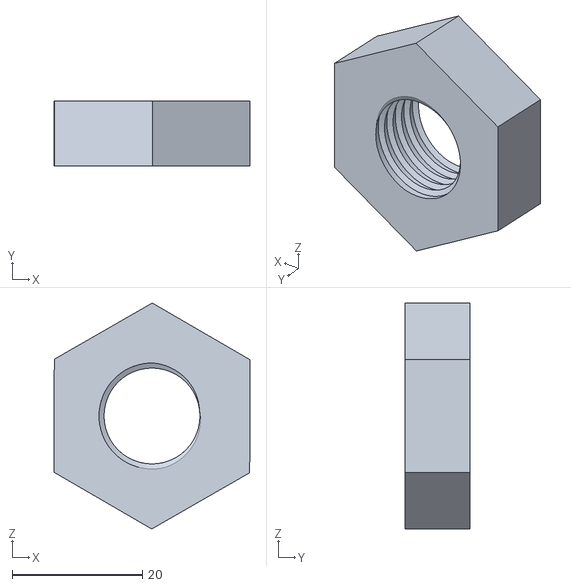
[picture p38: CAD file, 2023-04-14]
hardware/models/bulkhead nut.stl
30.0 x 10.0 x 34.6

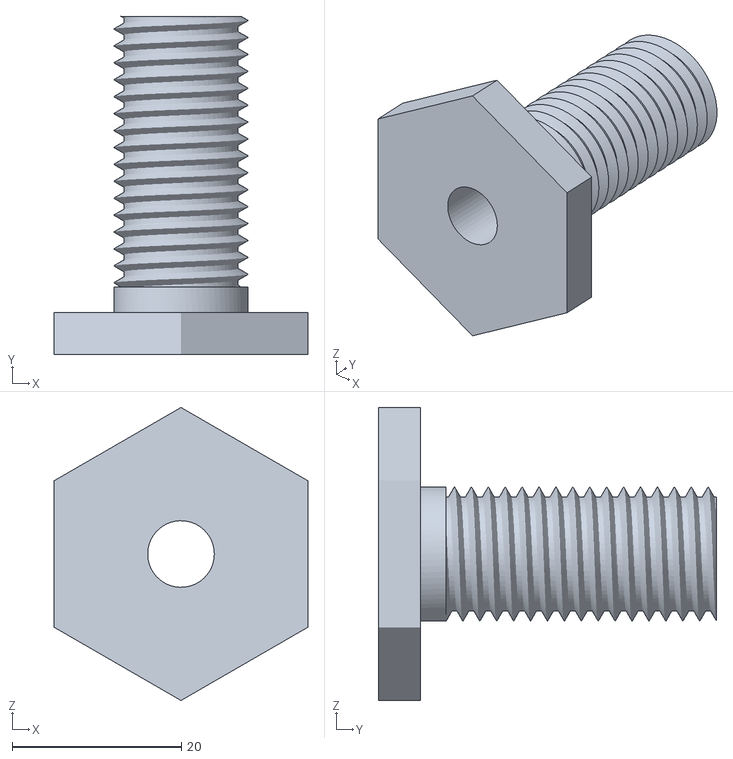
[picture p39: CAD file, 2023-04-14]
hardware/models/bulkhead bolt.stl
30.0 x 40.0 x 34.6

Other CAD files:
hardware/models/3-8 thread to 3-4 thread.stl
hardware/models/bulkhead and adapters.f3d
hardware/models/controller case.f3d
hardware/models/flow_sensor_case.f3d
hardware/models/pressure case.f3d
hardware/models/valve case.f3d

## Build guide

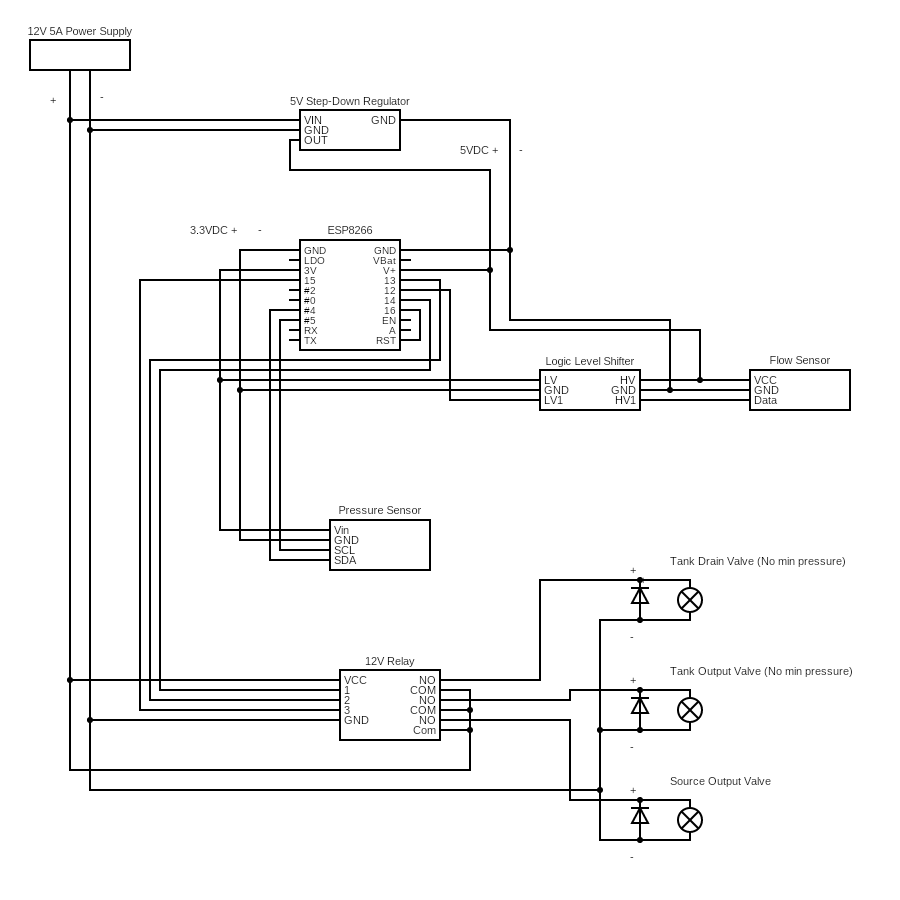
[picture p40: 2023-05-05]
docs/images/assembly/circuit_diagram.png

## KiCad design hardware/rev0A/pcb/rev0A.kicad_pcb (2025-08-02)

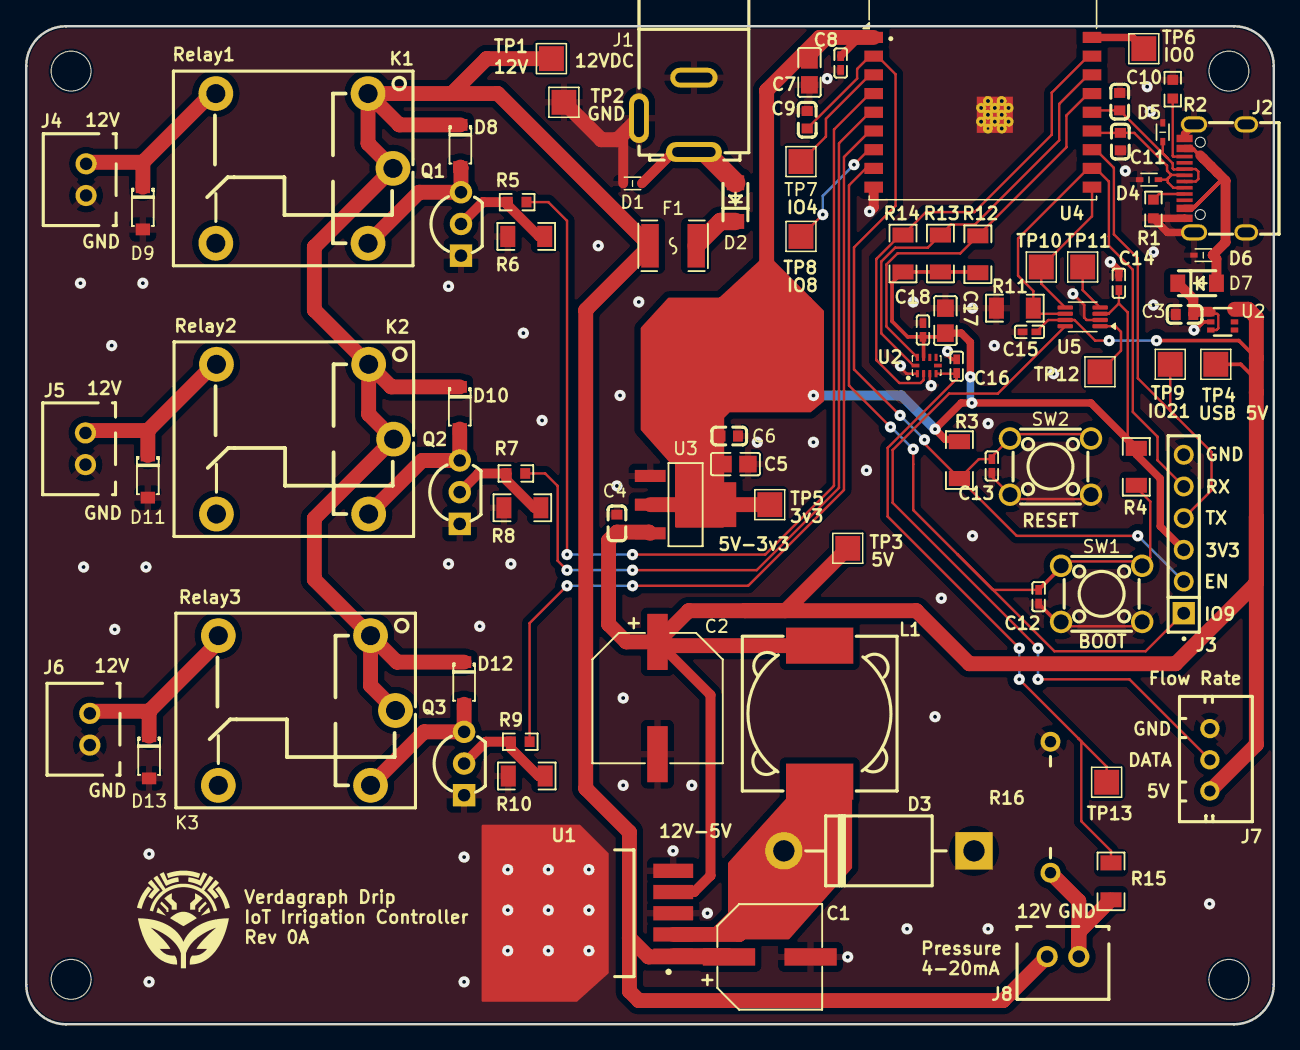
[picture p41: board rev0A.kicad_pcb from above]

Board: 2 copper layers, 100.0 x 80.0 mm, 84 parts (0 on the bottom side), 41 nets.

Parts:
C1: 100uF; CAP-SMD_BD8.0-L8.3-W8.3-FD
C2: 330uF; CAP-SMD_BD10.0-L10.3-W10.3-LS11.3-FD
C3, C4, C6, C9: 1uF; C0603
C5, C7, C17: 10uF; C0805
C8, C12, C13, C14, C15, C16, C18: 0.1uF; C0402
C10, C11: 22pF; C0603
D1, D4, D5, D6: LESD5D5.0CT1G; SOD-523_L1.2-W0.8-LS1.6-BI
D2, D7: MBR230LSFT1G; SOD-123FL_L2.8-W1.8-LS3.6-RD
D3: 1N5822; DO-201AD_BD5.3-L8.4-P12.50-D1.4-FD
D8, D9, D10, D11, D12, D13: 1N4148W; SOD-123_L2.8-W1.8-LS3.7-RD
F1: 1A; F1812
J1: EJ508A; DC-IN-TH_EJ508A
J2: TYPE-C-31-M-12; USB-C_SMD-TYPE-C-31-M-12
J3: 6 Pin Socket Header; HDR-TH_6P-P2.54-V-F
J4, J5, J6, J8: 2 Pin JST; CONN-TH_B2B-XH-A-LF-SN
J7: 3 Pin JST; CONN-TH_3P-P2.50_A2501WV2-3P
K1, K2, K3: SRD-12VDC-SL-C; RELAY-TH_SRD-XXVDC-XL-C
L1: 330uH; IND-SMD_L12.3-W12.3
Q1, Q2, Q3: BC337; TO-92-3_L4.8-W3.7-P2.54-R
R1, R2: 5100; R0603
R3, R4, R6, R8, R10, R11, R12, R13, R14, R15: 10000; R1206
R5, R7, R9: 1000; R0603
R16: 120; RES-TH_BD2.2-L6.5-P10.50-D0.6
SW1, SW2: SW_Push; SW-TH_4P-L6.0-W6.0-P4.50-LS6.5
TP1, TP2, TP6, TP7, TP8, TP9: TestPoint_Pad_2.0x2.0mm
TP3, TP4, TP5, TP10, TP11, TP12, TP13: TestPoint; TestPoint_Pad_2.0x2.0mm
U1: LM2575T-5.0; TO-263-5_L10.2-W8.9-P1.70-TL
U2: TPS22919QDCKRQ1; SC-70-6_L2.0-W1.3-P0.65-LS2.1-BR
U3: LDL1117S33R; SOT-223-4_L6.5-W3.5-P2.30-LS7.0-BR
U4: ESP32-C3-WROOM-02-H4; ESP32-C3-WROOM-02
U5: TXS0102DCU; VSSOP-8_2.3x2mm_P0.5mm
U6: ADS1115IRUGT; X2QFN-10_L2.0-W1.5-P0.50-TL_RUG0010B

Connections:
+3.3V: C5.1, C6.1, C7.2, C8.2, C14.2, C17.1, C18.1, J3.3, R3.1, R4.1, R12.2, R13.2, R14.2, TP5.1, U3.2 (VOUT), U3.4 (VOUT), U4.1 (3V3), U5.3 (VCCA), U6.8 (VDD)
+5V: C2.1, C4.1, C15.1, J7.1, L1.2, TP3.1, TP4.1, U1.4 (FB), U2.6 (VOUT), U3.3 (VIN), U5.7 (VCCB)
+12V: C1.1, D8.1 (K), D10.1 (K), D12.1 (K), F1.2, J8.1, K1.C1, K1.COM, K2.C1, K2.COM, K3.C1, K3.COM, TP1.1, U1.1 (VIN)
ADC Alert: R14.1, U4.17 (IO1), U6.2 (ALERT/RDY)
CHIP_PU: C9.1, C13.1, J3.2, R3.2, SW2.3, SW2.4, U4.2 (EN)
D+: C10.1, D5.2, J2.A6 (DP1), J2.B6 (DP2), U4.14 (IO19)
D-: C11.1, D4.2, J2.A7 (DN1), J2.B7 (DN2), U4.13 (IO18)
Flow Sensor Data: TP10.1, U4.10 (IO10), U5.5 (A1)
Flow Sensor Enable: J3.5, R11.2, U4.11 (IO20/RXD), U5.6 (OE)
GND: C1.2, C2.2, C3.2, C4.2, C5.2, C6.2, C7.1, C8.1, C9.2, C10.2, C11.2, C12.2, C13.2, C14.1, C15.2, C16.2, C17.2, C18.2, D1.1, D3.1 (A), D4.1, D5.1, D6.1, D9.2 (A), D11.2 (A), D13.2 (A), J1.2, J1.3, J2.A1 (GND), J2.A12 (GND), J2.B1 (GND), J2.B12 (GND), J2.S1 (SHIELD), J2.S2 (SHIELD), J2.S3 (SHIELD), J2.S4 (SHIELD), J3.6, J4.2, J5.2, J6.2, J7.3, Q1.1 (E), Q2.1 (E), Q3.1 (E), R1.2, R2.2, R6.2, R8.2, R10.2, R11.1, R16.2, SW1.1, SW1.2, SW2.1, SW2.2, TP2.1, U1.3 (GND), U1.5 (~ON/OFF), U1.6 (TAB(GND)), U2.2 (GND), U3.1 (GND), U4.9 (GND), U4.19 (GND), U5.2 (GND), U6.1 (ADDR), U6.3 (GND)
GPIO9: C12.1, J3.1, R4.2, SW1.3, SW1.4, U4.8 (IO9)
IO21: J3.4, TP9.1, U4.12 (IO21/TXD)
unnamed: D1.2, D2.2 (A), J1.1
unnamed: D2.1 (K), F1.1
unnamed: D3.2 (K), L1.1, U1.2 (OUT)
unnamed: D6.2, D7.2 (A), J2.A4 (VBUS), J2.A9 (VBUS), J2.B4 (VBUS), J2.B9 (VBUS)
unnamed: C3.1, D7.1 (K), U2.1 (IN), U2.3 (ON)
unnamed: D8.2 (A), K1.C2, Q1.3 (C)
unnamed: D9.1 (K), J4.1, K1.NO
unnamed: D10.2 (A), K2.C2, Q2.3 (C)
unnamed: D11.1 (K), J5.1, K2.NO
unnamed: D12.2 (A), K3.C2, Q3.3 (C)
unnamed: D13.1 (K), J6.1, K3.NO
unnamed: J2.A5 (CC1), R1.1
unnamed: J2.B5 (CC2), R2.1
unnamed: J7.2, U5.8 (B1)
unnamed: J8.2, R15.2, R16.1
unnamed: Q1.2 (B), R5.2, R6.1
unnamed: Q2.2 (B), R7.2, R8.1
unnamed: Q3.2 (B), R9.2, R10.1
unnamed: TP6.1, U4.18 (IO0)
unnamed: TP7.1, U4.3 (IO4)
unnamed: TP8.1, U4.7 (IO8)
unnamed: TP11.1, U5.4 (A2)
unnamed: TP12.1, U5.1 (B2)
unnamed: C16.1, R15.1, TP13.1, U6.4 (AIN0)
Relay1: R5.1, U4.4 (IO5)
Relay2: R7.1, U4.5 (IO6)
Relay3: R9.1, U4.6 (IO7)
SCLK: R13.1, U4.16 (IO2), U6.10 (SCL)
SDA: R12.1, U4.15 (IO3), U6.9 (SDA)

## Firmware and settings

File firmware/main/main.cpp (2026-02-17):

#include <stdio.h>
#include "freertos/FreeRTOS.h"
#include "freertos/task.h"

#include "mainStateController.h"

/** Main task stack size, in words (4 bytes on Esp32c3) */
constexpr size_t STACK_SIZE = 512U;

/**
 * @brief Runs the finite state machine.
 * 
 * @param pvParameters Allows parameters to be passed from the main function. Currently unused. 
 */
void vMainTask(void *pvParameters) {
    DataContainer dataContainer = DataContainer();
    ConfigManager configManager = ConfigManager(dataContainer);
    //MqttManager mqttManager(dataContainer);
    //WifiManager wifiManager(dataContainer);
    //ValveManager valveManager(dataContainer);
    //FlowSensorManager flowSensorManager;

    /** Initialize the FSM. */
    MainStateController mainStateController = MainStateController(
        dataContainer,
        configManager
        //wifiManager,
        //mqttManager,
        //valveManager,
        //flowSensorManager
    );
    
    /** Run the FSM. */
    while (true) {
        mainStateController.update();
    }

    /** Should not reach here. */
    vTaskDelete( NULL );
}

/**
 * @brief Entrypoint. 
 */
extern "C" void app_main(void) {
    BaseType_t xReturned;
    TaskHandle_t xHandle = NULL;

    /** Run task through FreeRTOS. */
    xReturned = xTaskCreate(vMainTask, 
        "FSM", 
        STACK_SIZE, 
        (void*) nullptr, 
        tskIDLE_PRIORITY, 
        &xHandle
    );

    /** Should not reach here. */
    if (xReturned == pdPASS) {
        vTaskDelete(xHandle);
    }
}

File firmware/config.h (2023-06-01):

// config.h
#ifndef CONFIG_H
#define CONFIG_H

#include <cstring>

// *************
// ************* See the documentation for detailed
// ************* descriptions about what each of the 
// ************* config settings does!
// *************


// ************* Core ************* //
// *************
// ************* This group of settings are key configs that describe specific
// ************* physical and electrical assumptions about the device.
// ************* They enable/disable functions (mqtt topics, services)
// ************* Read the documentation before setting these!
// *************

#define DEBUG true
#define SLOG if(DEBUG)Serial

#define RESEVOIR_MODE 1
#define USING_SOURCE_FLOW true
#define USING_DRAIN_VALVE true
#define USING_PRESSURE_SENSOR false


// ************* WiFiManager AutoConnect config ************* //

#define AP_NAME "irrigation_controller"
#define AP_PASSWORD "verdantech"
#define AP_IP IPAddress(192, 168, 0, 0)
#define AP_GATEWAY IPAddress(192, 168, 0, 1)
#define AP_SUBNET IPAddress(255, 255, 255, 0)
#define AP_TIMEOUT 120
#define AP_RETRY_DELAY 360
#define AP_RETRY_DEEP_SLEEP true


// ************* MQTT network config ************* //

#define MQTT_SERVER_DOMAIN_DEFAULT "192.168.0.195"
#define MQTT_SERVER_PORT_DEFAULT "1883"
#define MQTT_ID_DEFAULT "irrigation_controller1"
#define MQTT_USE_CREDENTIALS false
#define MQTT_USERNAME_DEFAULT "irrigation"
#define MQTT_PASSWORD_DEFAULT "tank"
#define MQTT_RETRY_TIMEOUT 300
#define MQTT_MAX_BUFFER_SIZE 512
#define MQTT_KEEPALIVE 15


// ************* Pin config ************* //

#define SOURCE_OUTPUT_VALVE_PIN 14
#define TANK_OUTPUT_VALVE_PIN 15
#define TANK_DRAIN_VALVE_PIN 13
#define FLOW_SENSOR_PIN 12


// ************* Defaults ************* //
// *************
// ************* The following configs are defaults 
// ************* and can be changed during runtime 
// ************* through an MQTT topic
// *************

#define DATA_RESOLUTION_L_DEFAULT 0.2
#define STATIC_FLOW_RATE_DEFAULT 12.45
#define PULSES_PER_L_DEFAULT 1265.289
#define MAX_FLOW_RATE_DEFAULT 30
#define MIN_FLOW_RATE_DEFAULT 0.2
#define FLOW_CALIBRATION_TIMEOUT 30
#define FLOW_CALIBRATION_MAX_VOLUME 0.5
#define TANK_TIMEOUT_DEFAULT 10
#define TANK_SHAPE_DEFAULT 2
#define TANK_DIMENSION_1_DEFAULT 0.4
#define TANK_DIMENSION_2_DEFAULT 1.2
#define TANK_DIMENSION_3_DEFAULT 0
#define PRESSURE_REPORT_MODE_DEFAULT 3
#define ATMOSPHERIC_PRESSURE_HPA_DEFAULT 1013.25


// ************* MQTT topic config ************* //

#define BASE_TOPIC "VD1/"
#define DISPENSE_ACTIVATE_TOPIC "out/on"
#define DISPENSE_REPORT_SLICE_TOPIC "out/log/sl"
#define DISPENSE_REPORT_SUMMARY_TOPIC "out/log/sm"
#define DEACTIVATE_TOPIC "off"
#define RESTART_TOPIC "restart"
#define LOG_TOPIC "log/info"
#define WARNING_TOPIC "log/warning"
#define ERROR_TOPIC "log/error"
#define CONFIG_TOPIC "config"
#define AUTO_CONFIG_TOPIC "config/auto" 
#define TOPIC_CONFIG_TOPIC "topics"
#define CONFIG_CHANGE_TOPIC "config/change"
#define SETTINGS_RESET_TOPIC "config/reset"
#define FLOW_SENSOR_CALIBRATE_BEGIN_TOPIC "flow/calibrate"
#define FLOW_SENSOR_CALIBRATE_DISPENSE_TOPIC "flow/dispense"
#define FLOW_SENSOR_CALIBRATE_MEASURE_TOPIC "flow/measure"
#define DRAIN_ACTIVATE_TOPIC "drain/on"
#define DRAIN_REPORT_SUMMARY_TOPIC "drain/log"
#define PRESSURE_REQUEST_TOPIC "pressure/request"
#define PRESSURE_REPORT_TOPIC "pressure/report"


// ************* Auto-config ************* //
// *************
// ************* This group of settings are automatically configured.
// ************* Don't change unless willing to modify code!
// *************

// ************* Operating mode ************* //
#define USING_SOURCE_ ((RESEVOIR_MODE == 1 || RESEVOIR_MODE == 3) ? true : false)
#define USING_TANK_ ((RESEVOIR_MODE == 2 || RESEVOIR_MODE == 3) ? true : false)
#define USING_DRAIN_VALVE_ ((USING_TANK_ && USING_DRAIN_VALVE) ? true : false)
#define USING_FLOW_SENSOR_ ((USING_TANK_ || USING_SOURCE_FLOW) ? true : false)
#define USING_PRESSURE_SENSOR_ ((USING_TANK_ && USING_PRESSURE_SENSOR) ? true : false)

// ************* Pins ************* //
// Define pins to -1 to indicate non-use based on operational mode
#define SOURCE_OUTPUT_VALVE_PIN_ (USING_SOURCE_ ? SOURCE_OUTPUT_VALVE_PIN : -1)
#define TANK_OUTPUT_VALVE_PIN_ (USING_TANK_ ? TANK_OUTPUT_VALVE_PIN : -1)
#define TANK_DRAIN_VALVE_PIN_ (USING_DRAIN_VALVE_ ? TANK_DRAIN_VALVE_PIN : -1)
#define FLOW_SENSOR_PIN_ (USING_FLOW_SENSOR_ ? FLOW_SENSOR_PIN : -1)
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

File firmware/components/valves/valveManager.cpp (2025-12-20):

#include "esp_err.h"
#include "freertos/task.h"

#include "valveManager.h"
#include "rxMessages.h"

static const char* TAG = "ValveManager";

/**
 * @brief State handler map.
 */
constexpr StateHandlerMapPair<DripValveManagerStateId_e, ValveManager> stateToHandlerMapValues[] {
    etl::pair{
        DripValveManagerStateId_e::Idle, 
        StateHandlerMapEntry_t<ValveManager>{
            &ValveManager::idleEntry, 
            &ValveManager::idleUpdate, 
            &ValveManager::idleUpdate,
        }
    },
    etl::pair{
        DripValveManagerStateId_e::DispenseStart, 
        StateHandlerMapEntry_t<ValveManager>{
            &ValveManager::dispenseStartEntry, 
            &ValveManager::dispenseStartUpdate, 
            &ValveManager::dispenseStartExit, 
        },
    },
    etl::pair{
        DripValveManagerStateId_e::DispenseSource, 
        StateHandlerMapEntry_t<ValveManager>{
            &ValveManager::dispenseSourceEntry, 
            &ValveManager::dispenseSourceUpdate, 
            &ValveManager::dispenseSourceExit, 
        },
    },
    etl::pair{
        DripValveManagerStateId_e::DispenseTank, 
        StateHandlerMapEntry_t<ValveManager>{
            &ValveManager::dispenseTankEntry, 
            &ValveManager::dispenseTankUpdate, 
            &ValveManager::dispenseTankExit, 
        },
    },
    etl::pair{
        DripValveManagerStateId_e::DispenseExit, 
        StateHandlerMapEntry_t<ValveManager>{
            &ValveManager::dispenseExitEntry, 
            &ValveManager::dispenseExitUpdate, 
            &ValveManager::dispenseExitExit, 
        },
    },
    etl::pair{
        DripValveManagerStateId_e::DrainTank, 
        StateHandlerMapEntry_t<ValveManager>{
            &ValveManager::drainTankEntry, 
            &ValveManager::drainTankUpdate, 
            &ValveManager::drainTankExit, 
        },
    },
    etl::pair{
        DripValveManagerStateId_e::Deactivate, 
        StateHandlerMapEntry_t<ValveManager>{
            &ValveManager::deactivateEntry, 
            &ValveManager::deactivateUpdate, 
            &ValveManager::deactivateExit, 
        },
    },
};
using FsmStateMap = StateHandlerMap<DripValveManagerStateId_e, ValveManager>;
constexpr FsmStateMap stateToHandlerMap { stateToHandlerMapValues };

/**
 * @brief Event handler map.
 */
constexpr EventHandlerMapPair<DripValveManagerStateId_e, DripValveManagerEventId_e, DripRxMessage<DripValveManagerEventId_e>, ValveManager> eventToHandlerMapValues[] {
    etl::pair{
        EventHandlerMapKey_t<DripValveManagerStateId_e, DripValveManagerEventId_e>(
            DripValveManagerStateId_e::Idle, 
            DripValveManagerEventId_e::DispenseStart
        ),
        EventHandlerMapEntry_t<DripValveManagerEventId_e, DripRxMessage<DripValveManagerEventId_e>, ValveManager>(
            &ValveManager::handleDispenseRequestStateIdle
        )
    },
    etl::pair{
        EventHandlerMapKey_t<DripValveManagerStateId_e, DripValveManagerEventId_e>(
            DripValveManagerStateId_e::DispenseStart, 
            DripValveManagerEventId_e::Deactivate
        ),
        EventHandlerMapEntry_t<DripValveManagerEventId_e, DripRxMessage<DripValveManagerEventId_e>, ValveManager>(
            &ValveManager::handleDeactivateRequestStateDispenseOrDrain
        )
    },
    etl::pair{
        EventHandlerMapKey_t<DripValveManagerStateId_e, DripValveManagerEventId_e>(
            DripValveManagerStateId_e::DispenseSource, 
            DripValveManagerEventId_e::Deactivate
        ),
        EventHandlerMapEntry_t<DripValveManagerEventId_e, DripRxMessage<DripValveManagerEventId_e>, ValveManager>(
            &ValveManager::handleDeactivateRequestStateDispenseOrDrain
        )
    },
    etl::pair{
        EventHandlerMapKey_t<DripValveManagerStateId_e, DripValveManagerEventId_e>(
            DripValveManagerStateId_e::DispenseTank, 
            DripValveManagerEventId_e::Deactivate
        ),
        EventHandlerMapEntry_t<DripValveManagerEventId_e, DripRxMessage<DripValveManagerEventId_e>, ValveManager>(
            &ValveManager::handleDeactivateRequestStateDispenseOrDrain
        )
    },
    etl::pair{
        EventHandlerMapKey_t<DripValveManagerStateId_e, DripValveManagerEventId_e>(
            DripValveManagerStateId_e::DrainTank, 
            DripValveManagerEventId_e::Deactivate
        ),
        EventHandlerMapEntry_t<DripValveManagerEventId_e, DripRxMessage<DripValveManagerEventId_e>, ValveManager>(
            &ValveManager::handleDeactivateRequestStateDispenseOrDrain
        )
    },
    etl::pair{
        EventHandlerMapKey_t<DripValveManagerStateId_e, DripValveManagerEventId_e>(
            DripValveManagerStateId_e::Idle, 
            DripValveManagerEventId_e::DrainStart
        ),
        EventHandlerMapEntry_t<DripValveManagerEventId_e, DripRxMessage<DripValveManagerEventId_e>, ValveManager>(
            &ValveManager::handleDrainRequestStateIdle
        )
    },
};
using FsmEventMap = EventHandlerMap<DripValveManagerStateId_e, DripValveManagerEventId_e, DripRxMessage<DripValveManagerEventId_e>, ValveManager>;
constexpr FsmEventMap eventToHandlerMap { eventToHandlerMapValues };

ValveManager::ValveManager(
    DataContainer &dataContainer
) : 
    StateController<DripValveManagerStateId_e, DripValveManagerEventId_e, DripRxMessage<DripValveManagerEventId_e>, ValveManager>(
        DripValveManagerStateId_e::Idle,
        "MainFsm",
        stateToHandlerMap,
        eventToHandlerMap,
        *this,
        dataContainer
    ),

    eventTimers_{},
    dataContainer_(dataContainer),
    openValve_(DripValves_e::Null) {}

esp_err_t ValveManager::initialize() {
    return ESP_OK;
}

bool ValveManager::isIdle() const {
    if (DripValveManagerStateId_e::Idle == machine_.getCurrentState() ) {
        return true;
    } else {
        return false;
    }
}
bool ValveManager::isDispensing() const {
    if ( 
        (DripValveManagerStateId_e::DispenseStart == machine_.getCurrentState() ) || 
        (DripValveManagerStateId_e::DispenseSource == machine_.getCurrentState() ) || 
        (DripValveManagerStateId_e::DispenseTank == machine_.getCurrentState() ) ) {
        return true;
    } else {
        return false;
    }
}
bool ValveManager::isDraining() const {
    if (DripValveManagerStateId_e::DrainTank == machine_.getCurrentState() ) {
        return true;
    } else {
        return false;
    }
}

/**
 * @brief Handlers for state idle.
 */
void idleEntry();
void idleUpdate();
void idleExit();
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

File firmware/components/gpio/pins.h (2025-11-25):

#ifndef PINS_H
#define PINS_H

constexpr bool DRIP_GPIO_PIN_ENABLE = true;
constexpr bool DRIP_GPIO_PIN_DISABLE = false;

constexpr gpio_num_t DRIP_GPIO_PIN_I2C_SDA = GPIO_NUM_0;
constexpr gpio_num_t DRIP_GPIO_PIN_I2C_SCL = GPIO_NUM_0;

constexpr gpio_num_t DRIP_GPIO_PIN_RELAY1 = GPIO_NUM_0;
constexpr gpio_num_t DRIP_GPIO_PIN_RELAY2 = GPIO_NUM_0;
constexpr gpio_num_t DRIP_GPIO_PIN_RELAY3 = GPIO_NUM_0;

/** Addr pin pulled to GND. */
#define ADS111RUGT_I2C_ADDR 0b1001000U
#define ADS111RUGT_I2C_CLK_FREQ_HZ 50000U

#endif

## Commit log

2023-03-28 Network initialization
    [4 MHT thread.stl, bulk_hose.stl, bulk_hose_adapter.stl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]
2023-04-03 Working on reporting. Need to fix mqtt_client extern
    [app.h, config.h, controller.ino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]
2023-04-12 updated all the cads
    [3-8 thread to 3-4 thread.stl, 4 MHT thread.stl, bulk_hose.stl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]
2023-04-12 updated bulkhead to 1/4 poly
    [bulkhead and adapters.f3d, bulkhead to 1-4 poly.stl]
2023-04-12 update bulkhead to 1/4 poly
    [bulkhead and adapters.f3d, bulkhead to 1-4 poly.stl]
2023-04-12 bulkhead to 1/4 poly
    [bulkhead and adapters.f3d, bulkhead to 1-4 poly.stl]
2023-04-14 Added flow sensor calibration
2023-04-27 update docs and cads
    [pressure case bottom.stl, pressure case middle.stl, pressure case.f3d]
2023-06-01 began PCB
    [kicad.kicad_pcb, kicad.kicad_sch]
2025-04-13 PCB draft
    [3-8 thread to 3-4 thread.stl, bulkhead and adapters.f3d, bulkhead bolt.stl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]
2025-04-20 PCB Progress
    [rev0A.kicad_pcb, rev0A.kicad_sch, test_bom.csv]
2025-04-24 Completes most PCB routing
    [rev0A.kicad_pcb, rev0A.kicad_sch]
2025-04-25 Completes PCB and drafts firmware structure
    [bom.csv, rev0A.kicad_pcb]
2025-04-27 PCB needs some final polish, adds structure of FSM and other managers
    [rev0A.kicad_pcb]
2025-04-27 Structured valve setup
2025-04-28 Polishing valve manager
2025-04-29 Updates PCB and readmes
    [rev0A-B_Cu.gbr, rev0A-B_Mask.gbr, rev0A-B_Paste.gbr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]
2025-05-06 Updated pcb screenshot
    [rev0A.kicad_pcb]
2025-06-27 Polishes PCB
    [rev0A-B_Cu.gbr, rev0A-B_Mask.gbr, rev0A-B_Paste.gbr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]
2025-08-02 Rev0A of the PCB
    [bom.csv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]
2025-11-11 Fills some more out
    [partition_custom.csv]
2025-11-23 Switche d to Plantfor mi IDOO
2025-11-25 Added new message framework
2025-12-08 Improving valve manager
